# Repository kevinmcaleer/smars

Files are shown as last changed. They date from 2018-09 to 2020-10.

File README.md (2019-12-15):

# SMARS

Screwless Modular Assemblable Robotic System



## SMARSfan.com

Visit www.smarsfan.com for more information about this project. The site includes build instructions, videos, an interview with the designer and much more.

## SMARSLab & SMARS_Library

I've broken the SMARS code into two parts:

SMARS_Library is a component that can now be installed via

```console
pip install smars-library
```

 or visiting <https://pypi.org/project/smars-library/>

SMARSLab is a web-based application for controlling your SMARS robots. The aim it that this will support both bluetooth connected wheeled SMARS as well as ones running locally on a raspberry pi zero. It currently supports QUAD SMARS and there is a test `butil.py` app for testing bluetooth connectivity.
Visit <https://www.github.com/kevinmcaleer/smarslab> for more information.

## About this library

This library will enable you to get the quad robot walking and detecting its environment.

## Python Library now pulls from pip

There is now a SMARS Python library available via pip.

***Make sure you follow the instructions below to ensure the virtual environment is setup correctly and everything should work perfectly.***

## Setup a virtual environment

The best way to ensure all the right prerequisites are installed and the supported version of python is installed is by setting up a virtual environment for python.

To Install virtualenv:

* log on to your raspberry pi
* install virtualenv:

```console
sudo apt-get install virtualenv
```

* create a new virtual python environment:

```console
virtualenv -p python3 venv
```

* activate the new python environment:

```console
source venv/bin/activate
```

* install the pre-requisites:

```console
pip install -r requirements.txt
```

* to deactivate the environment once you have finished, type

```console
deactivate
```

## Files

```.
├── Documentation                   - All the Documents
│   └── SMARS Build Instructions
│       └── Build instructions.pdf  - PDF version of the build instructions
├── limb_setup.py                   - script for helping setup limbs on a QUAD SMARS
├── pinouts.md                      - Describes the pinouts for the PCA9685
├── README.md                       - this file
├── requirements.txt                - used by pip to install the prerequisites
├── S-Code.md                       - a code similar to G-Code for sending commands to a SMARS, work in progress
├── S-CodeParse.py                  - a parser for S-Code
├── Scratch 1.4
│   └── SMARSScratchDemo.sb         - an example Scratch 1.4 file for communicating with SMARS
├── ScratchListener.py              - the lister app for communicating with SMARS and Scratch
├── setup.sh                        - a shell script for setting up the code on a raspberry pi
├── SMARS_ultrasonic_demo
│   └── SMARS_ultrasonic_demo.ino   - a sample Arduino script for using the ultrasonic sensor
├── STL_Files                       - some STL files for modified tracks
│   ├── Track 18mm.png
│   ├── Track 18mm.stl
│   ├── Track 20.5mm 16h.stl
│   ├── Track 20.5mm.stl
│   ├── Track 205mm.stl
│   ├── Track 210mm.stl
│   └── Track.png
└── test                            - the test suite
    ├── test.md                     - test suite documentation
    ├── test.py                     - a simple test app for checking your SMARS setup
    └── test_suite.py               - the test suite used by Travis-CI to confirm build quality
```

## Scratch 1.4 Code

The Library now includes a sample Scratch 1.4 script that will enable you to control your SMARS Quad robot from the scratch environment. Please note you will need to enable the remote sensor control for this to work, by right clicking on the sensor and clicking on 'enable remote sensing'.

The Scratch demo script needs to communicate with the Python 'ScratchListener.py' code, and you will need to know the IP address of the computer running Scratch 1.4.

Note only Scratch 1.4 has the 'enable remote sensing' option available, Scratch 2.0 & Scratch 3.0 do not allow this, however you can still download and use Scratch 1.4 from the Scratch website: <http://scratch.mit.edu>

Link to thingiverse original model:
<https://www.thingiverse.com/thing:2662828>

Link to Quad version
<https://www.thingiverse.com/thing:2755973>

## Overview and Background

This robot is really easy and cheap to 3d print, build and program. It can be assembled without screws or soldering and it's modular so it can be adapted for different purposes. I'm Swiss, so I don't know American scholastic system but I would use SMARS in last year of middle school, high school or universities/ colleges. There is more "open electronics" compared to a Lego NXT or similar, so students need a few knowledges about security, electrical laws and so on. It can be use to improve software development skills, CAD skills or electronics skills, students can design their own modules and customize their SMARS.

### Programming SMARS

You can use most common small hardware platforms as the brains inside SMARS, the Arduino platform (and compatible) was used in the original design as its cheap, commonly available, and the tools for programming it are easy to use. For the quad version of the robot a Raspberry Pi Zero was used. The language commonly used on the Pi (and where it gets it name from) is Python. A library module has been written for both Arduino and Python to help you get started.

### Getting the Arduino IDE

Visit <http://www.arduino.cc> to download the latest Arduino Integrated Development Environment (IDE).

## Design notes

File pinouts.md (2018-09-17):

This is the pinout connections for the Raspberry Pi to PCA9685 Servo Driver:

PCA9685 GND to RPI Pin 39 (or Pin 6)
PCA9685 V+ to RPI Pin 2
PCA9685 SCL to RPI Pin 5 (SCL)
PCA9685 SDA to RPI Pin 3 (SDA)

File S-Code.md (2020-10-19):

# S-Code

S-code describes a set of codes used to communicate with a SMARS robot.

An example sent over bluetooth would be:

```
S111 3
```

This would move the robot forward 3 units. A unit is dependent on lots of things so its hard to define in the language.

## Generic Movement

```
100 - # Movement
101 - Move Forward
102 - Move backward
103 - Turn left
104 - Turn right
```

## Wheeled SMARS

 ```
 110 - # Movement
 111 - Move Forward
 112 - Move Backwards
 113 - Turn Left
 114 - Turn Right
```

## Quad Smars

 ```
 150 - # Quad SMARS movements
 151 - Walk Forward
 152 - Walk Backward
 153 - Turn Left
 154 - Turn Right
 155 - Stand Up
 156 - Sit Down
 157 - Clap
 158 - Wiggle
```

## Inputs

```
200 - # Inputs, sensors
210 - Light sensor
211 - get light level
220 - Line sensor
221 - get light level
230 - Ultrasonic sensor
231 - get distance from sensor
240 - # Battery Level
241 - get battery level
250 - # IMU
251 - Get position from IMU
252 - Get Compass Heading
```

## Outputs

```
300 - # output - sound and lights
400 - status
401 - get current status
500 - Other Motors (for future use)
501 - Move motor 1
```

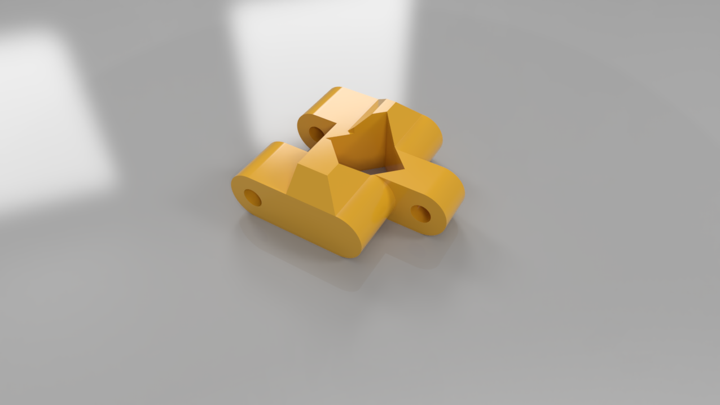
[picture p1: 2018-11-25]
STL_Files/Track 18mm.png

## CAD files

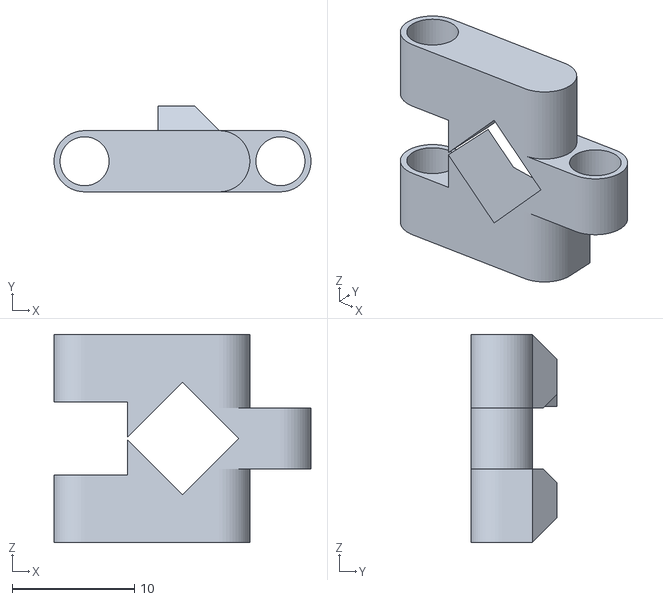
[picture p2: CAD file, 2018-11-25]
STL_Files/Track 210mm.stl
21.0 x 7.00 x 17.0

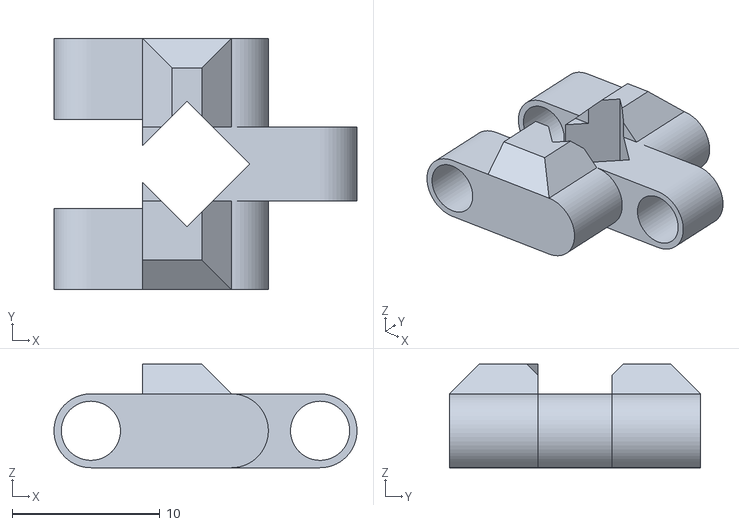
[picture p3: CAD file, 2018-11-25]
STL_Files/Track 20.5mm.stl
20.5 x 17.0 x 7.00

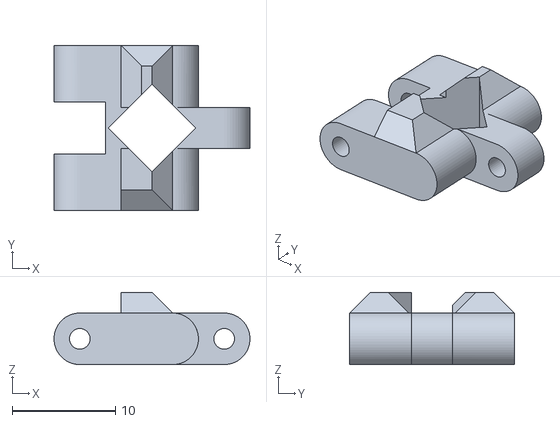
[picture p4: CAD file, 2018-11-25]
STL_Files/Track 18mm.stl
19.0 x 16.0 x 7.00

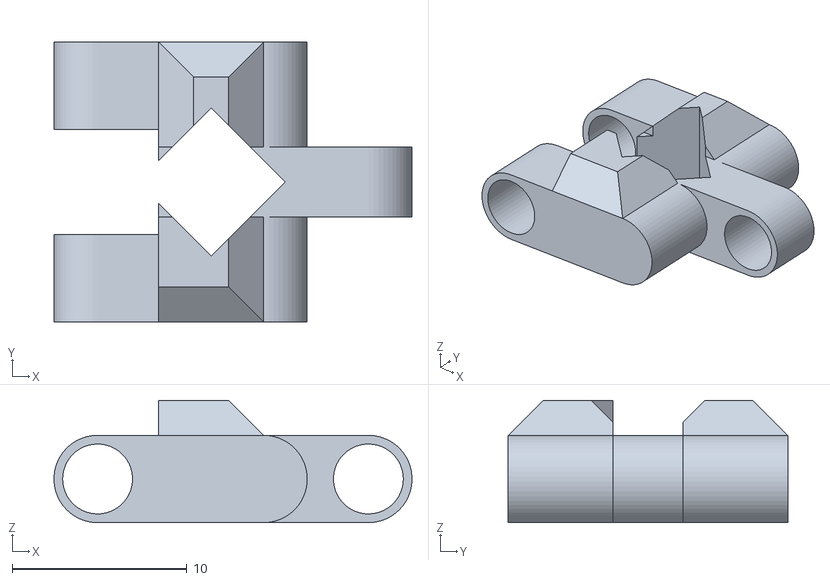
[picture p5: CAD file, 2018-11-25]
STL_Files/Track 20.5mm 16h.stl
20.5 x 16.0 x 7.00

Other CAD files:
STL_Files/Track 205mm.stl

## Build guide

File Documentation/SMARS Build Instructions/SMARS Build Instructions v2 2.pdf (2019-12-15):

# QUAD ROBOT WIRING DIAGRAM

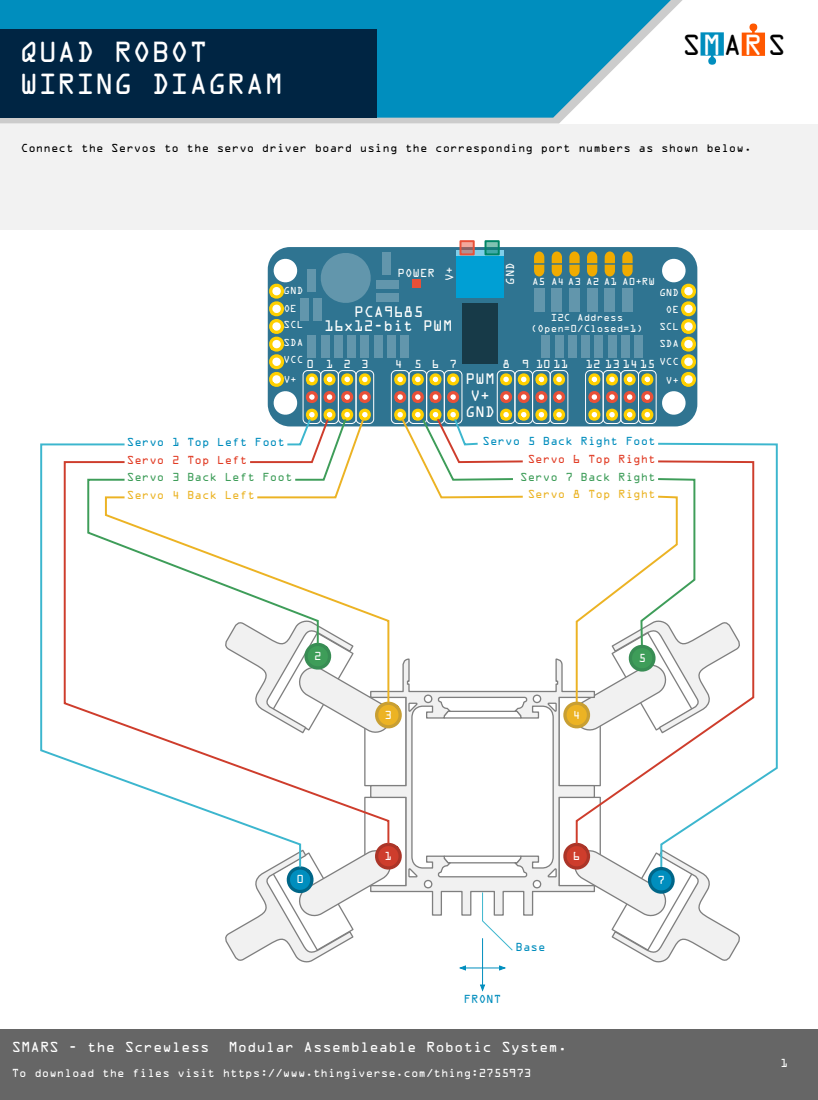
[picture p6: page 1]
SMAR S; SMARS - the Screwless; Modular Assembleable Robotic System.; GND; POWER; 16x12-bit PWM; PCA9685; PWM V+ GND; SCL; SDA; VCC; I2C Address (Open=0/Closed=1); Base; Servo 1 Top Left Foot; Servo 5 Back Right Foot; FRONT

Connect the Servos to the servo driver board using the corresponding port numbers as shown below.

Servo 2 Top Left
Servo 3 Back Left Foot
Servo 4 Back Left

Servo 6 Top Right
Servo 7 Back Right
Servo 8 Top Right

To download the files visit https://www.thingiverse.com/thing:2755973

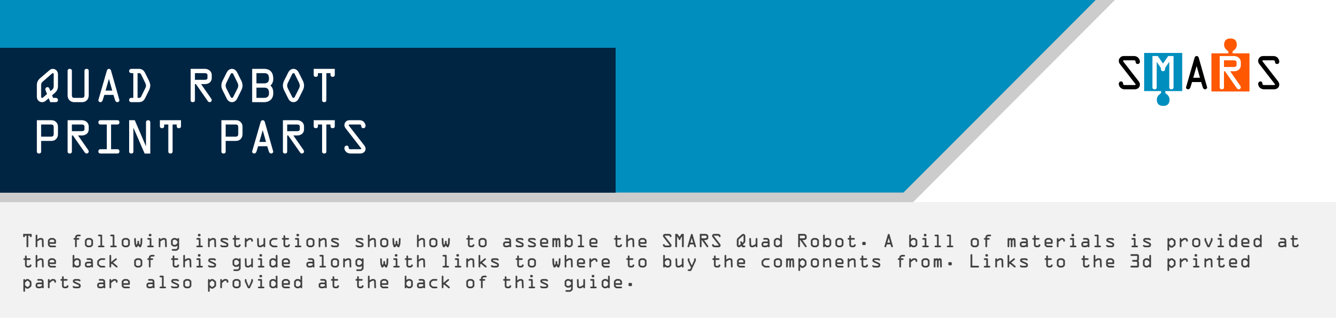
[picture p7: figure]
PRINT PARTS

1 | Print the frame
2 | Print the servo holders

Print 4x Servo holder & 4x Servo holder M (M is a mirror image of the servo holder)

SG90
Servo
Servo Holder | Servo Holder M
3 | Fit the servo into the servo holder

x8

4 Fit the servo holders into the frame

The following instructions show how to assemble the SMARS Quad Robot. A bill of materials is provided at the back of this guide along with links to where to buy the components from. Links to the 3d printed parts are also provided at the back of this guide.

# FITTING SERVOS

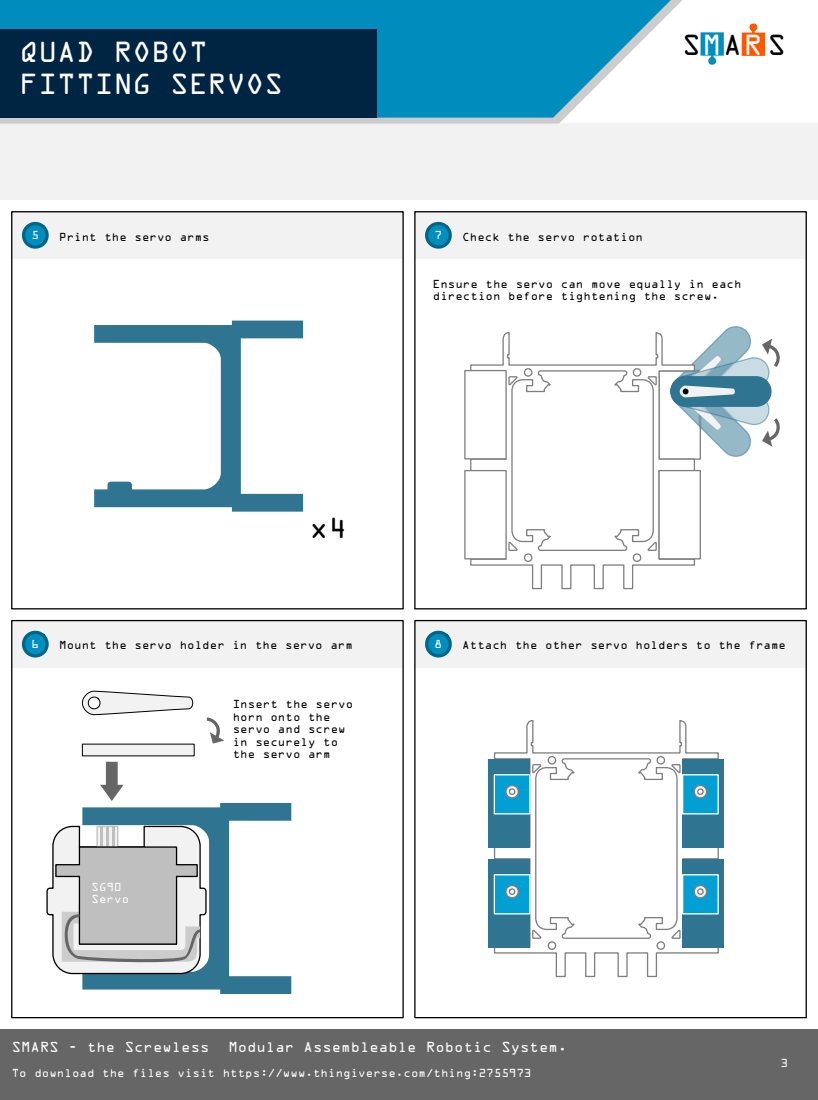
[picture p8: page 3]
Print the servo arms; Mount the servo holder in the servo arm; Check the servo rotation; Attach the other servo holders to the frame; SG90 Servo

Ensure the servo can move equally in each
direction before tightening the screw.

Insert the servo
horn onto the
servo and screw
in securely to
the servo arm

# FITTING THE FEET

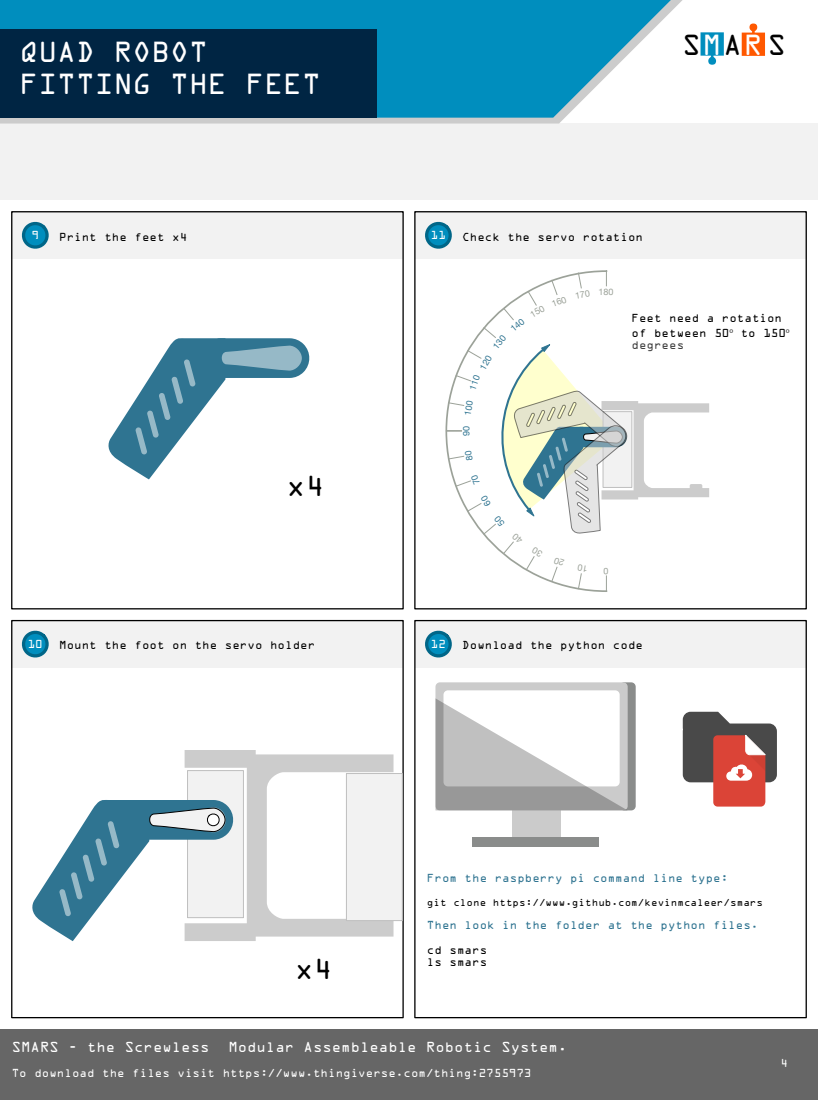
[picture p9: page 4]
Print the feet x4; Mount the foot on the servo holder; Check the servo rotation; Download the python code; cd smars ls smars

Feet need a rotation
of between 50º to 150º
degrees

From the raspberry pi command line type:

git clone https://www.github.com/kevinmcaleer/smars

Then look in the folder at the python files.

Connect the Raspberry pi Zero using the following pins:

PCA9685 GND to RPI Pin 39 (or Pin 6) - Black wire
PCA9685 V+ to RPI Pin 2 | - Red wire
PCA9685 SCL to RPI Pin 5 (SCL) | - Green wire
PCA9685 SDA to RPI Pin 3 (SDA) | - Blue wire

Note that the input voltage for the PCA9685 is 3.3v or 5v into the VCC. The V+ is for powering the servo motors and requires more power than the raspberry pi can provide, which is why it is separate. You can use a 9v battery to drive this, using the SMARS 9v case.

The raspberry pi communicates with the servo driver board using I2C, which only requires 2 wires: System Clock (SCL) and System Data (SDA). These are marked on servo driver board, and on pins 3 & 7 on the Raspberry Pi Zero.

# PI ZERO SETUP

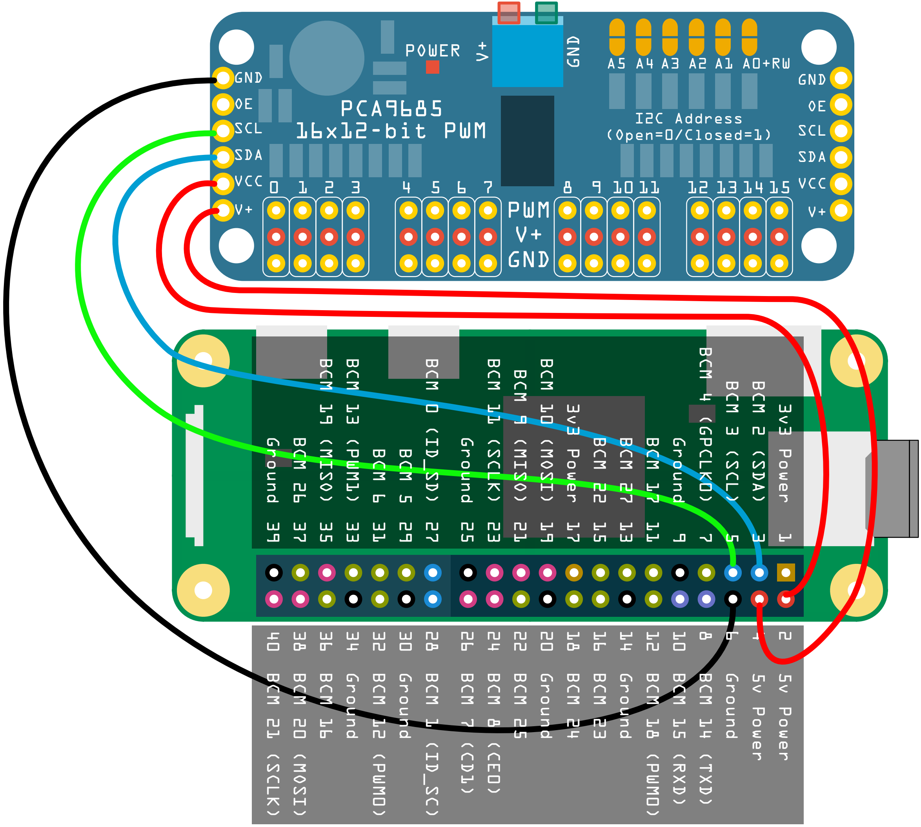
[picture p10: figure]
GND; POWER; 16x12-bit PWM; PCA9685; PWM V+ GND; SCL; SDA; VCC; I2C Address (Open=0/Closed=1); BCM 21 (SCLK); BCM 20 (MOSI); BCM 16; Ground; BCM 12 (PWM0); BCM 1 (ID_SC); BCM 7 (CD1); BCM 8 (CE0); BCM 25; BCM 24; BCM 23; BCM 18 (PWM0); BCM 15 (RXD); BCM 14 (TXD); 5v Power; 3v3 Power; BCM 3 (SCL); BCM 2 (SDA); BCM 4 (GPCLK0); BCM 22; BCM 27; BCM 17; BCM 10 (MOSI); BCM 9 (MISO); BCM 11 (SCLK); BCM 0 (ID_SD); BCM 6; BCM 5; BCM 19 (MISO); BCM 13 (PWM1); BCM 26

# RANGE OF MOTION

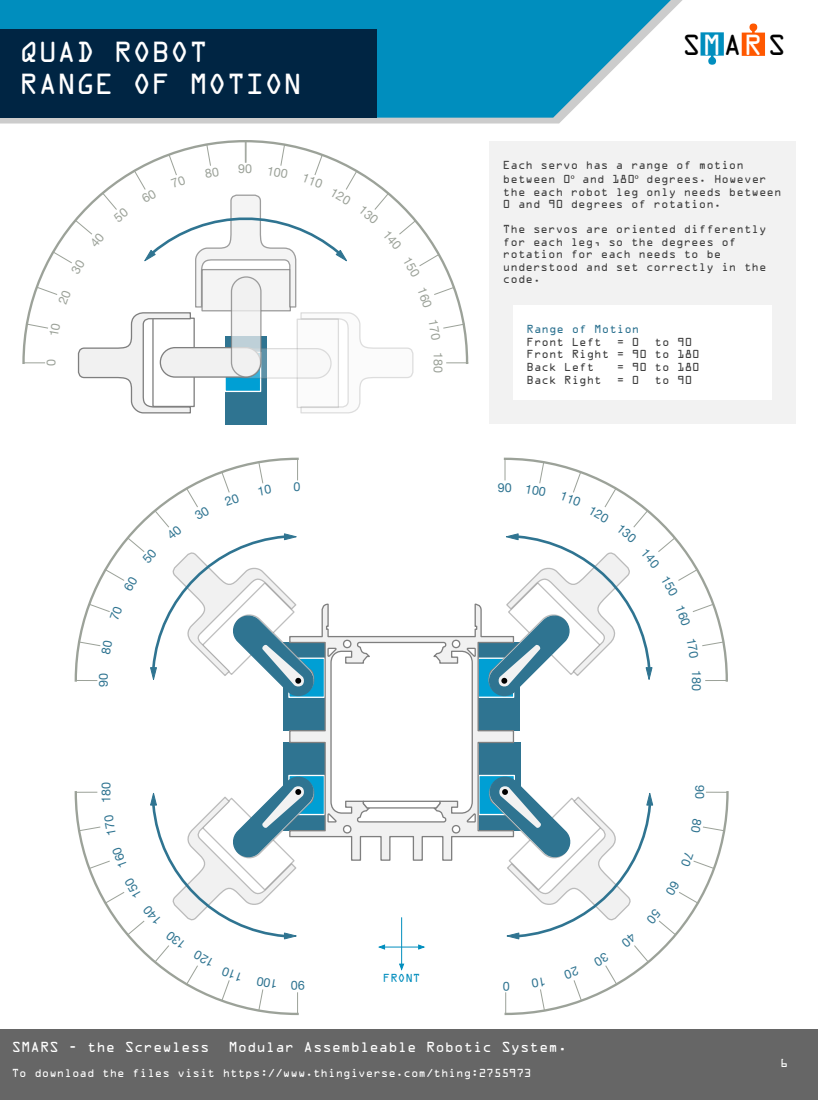
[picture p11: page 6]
Front Left; Back Left; Back Right; FRONT

Each servo has a range of motion
between 0º and 180º degrees. However
the each robot leg only needs between
0 and 90 degrees of rotation.

The servos are oriented differently
for each leg, so the degrees of
rotation for each needs to be
understood and set correctly in the
code.

Range of Motion
Front Right = 90 to 180

### Quad Robot Software Configuration

Once you’ve downloaded the python code you can begin checking the configuration of the servos:

### Python environment setup

The PCA9685 servo driver library is provided by Adafruit and needs to be installed before setup and using the SMARS Quad robot.

To download the adafruit servo library first logon to the Raspberry Pi and then type:

sudo apt-get install git build-essential python-dev cd ~
git clone https://github.com/adafruit/Adafruit_Python_PCA9685.git
cd Adafruit_Python_PCA9685
sudo python setup.py install

### Python is now setup for the servo

driver.

python limb_setup.py

### Use the menu to select the channel you want to configure. There are 16

channels, one for each servo.

The channels start at 0, and end at 15.

Menu
1) select channel
2) select angle
0) quit

current channel is: 0
current angle is: 0
enter number

Type ‘1’ to change the current channel.

Select Channel

currently selected channel is: 0
type channel number:, or q to return to the main menu

### Next, type 0 to configure channel 0

Type ‘1’ to change the current channel.

Select Channel

currently selected channel is: 0
type channel number:, or q to return to the main menu

### Next, type ‘0’ to configure channel 0

### Then type ‘q’ to return to the main

menu.

Menu
1) select channel
2) select angle
0) quit

current channel is: 0
current angle is: 0
enter number

### Type ‘2’ to set the angle for the

current channel.

Select Angle

current angle is: 0
Type angle to set servo to, or press q to exit90 90
Angle is: 90
Angle = | 90
Angle as a percentage = | 50.0
pulse = | 375
map Max = | 450
current angle: 90
Type angle to set servo to, or press q to exit

### Type ’90’ to set the angle to 90

Degrees.

### Then type ‘q’ to return to the main

menu.

### Repeat this until you have set each

limb correctly.

### Finally type ‘0’ to quit the limb setup

programme.

# SOFTWARE SETUP

### About this Guide

This guide was written by Kevin McAleer and is provided freely to the SMARS community.

### Social Media

If you haven’t already, please join the facebook community -https://www.facebook.com/groups/141101273276325/

# NEXT STEPS

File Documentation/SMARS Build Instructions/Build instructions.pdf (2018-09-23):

# QUAD ROBOT WIRING DIAGRAM

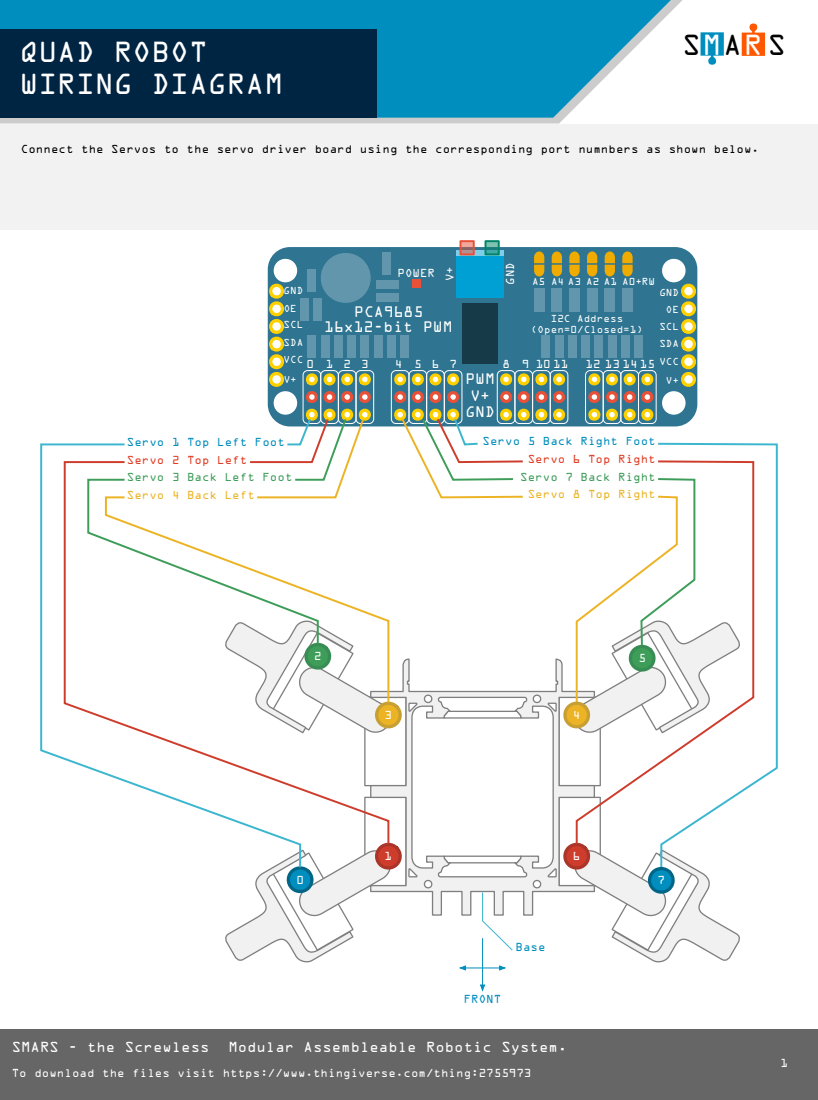
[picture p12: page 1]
SMAR S; SMARS - the Screwless; Modular Assembleable Robotic System.; GND; POWER; 16x12-bit PWM; PCA9685; PWM V+ GND; SCL; SDA; VCC; I2C Address (Open=0/Closed=1); Base; Servo 1 Top Left Foot; Servo 5 Back Right Foot; FRONT

Connect the Servos to the servo driver board using the corresponding port numnbers as shown below.

Servo 2 Top Left
Servo 3 Back Left Foot
Servo 4 Back Left

Servo 6 Top Right
Servo 7 Back Right
Servo 8 Top Right

To download the files visit https://www.thingiverse.com/thing:2755973

PRINT PARTS

1 | Print the frame
2 | Print the servo holders

Print 4x Servo holder & 4x Servo holder M (M is a mirror image of the servo holder)

SG90
Servo
Servo Holder | Servo Holder M
3 | Fit the servo into the servo holder

x8

4 Fit the servo holders into the frame

The following instructions show how to assemble the SMARS Quad Robot. A bill of materials is provided at the back of this guide along with links to where to buy the components from. Links to the 3d printed parts are also provided at the back of this guide.

# FITTING SERVOS

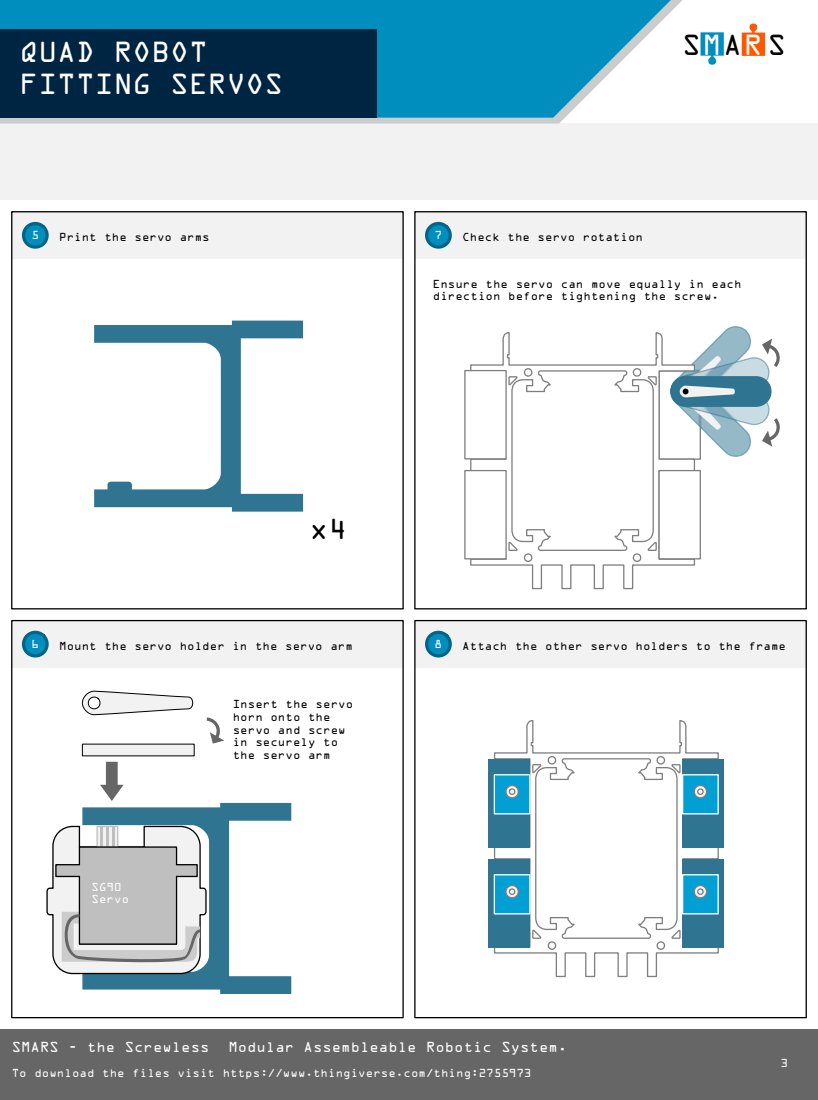
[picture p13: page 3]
Print the servo arms; Mount the servo holder in the servo arm; Check the servo rotation; Attach the other servo holders to the frame; SG90 Servo

Ensure the servo can move equally in each
direction before tightening the screw.

Insert the servo
horn onto the
servo and screw
in securely to
the servo arm

# FITTING THE FEET

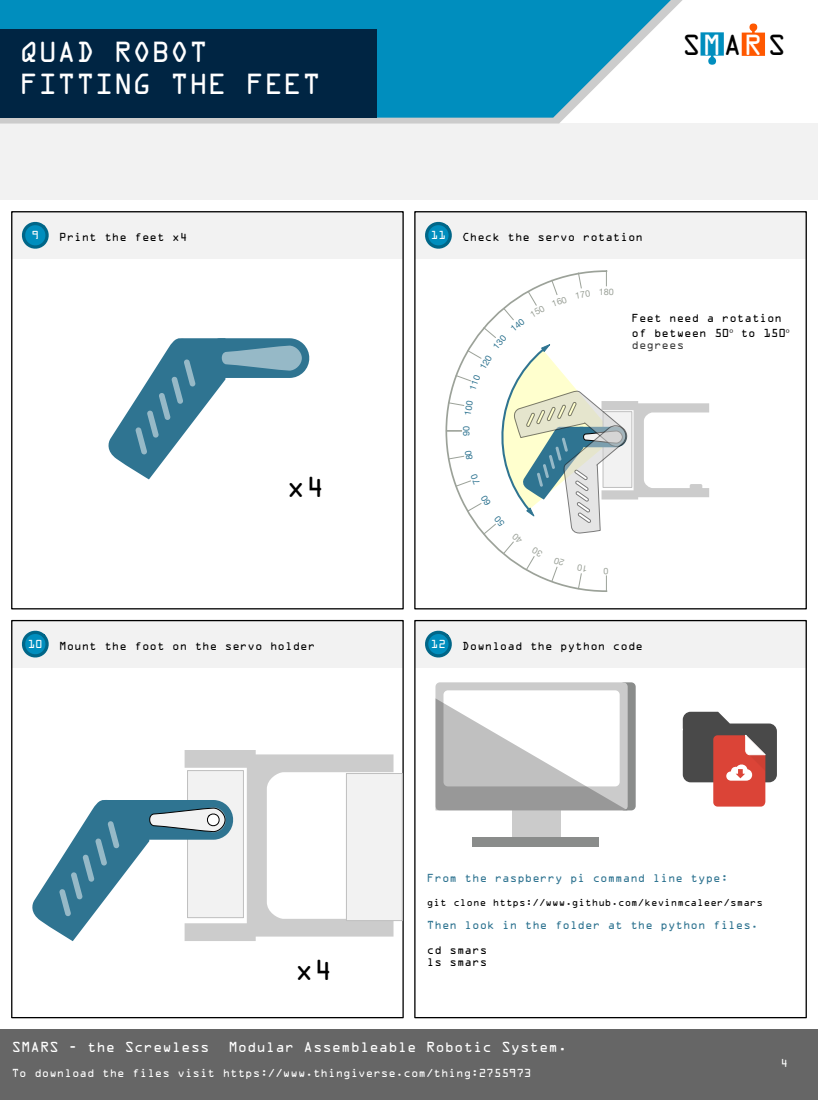
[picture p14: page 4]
Print the feet x4; Mount the foot on the servo holder; Check the servo rotation; Download the python code; cd smars ls smars

Feet need a rotation
of between 50º to 150º
degrees

From the raspberry pi command line type:

git clone https://www.github.com/kevinmcaleer/smars

Then look in the folder at the python files.

Connect the Raspberry pi Zero using the following pins:

PCA9685 GND to RPI Pin 39 (or Pin 6) - Black wire
PCA9685 V+ to RPI Pin 2 | - Red wire
PCA9685 SCL to RPI Pin 5 (SCL) | - Green wire
PCA9685 SDA to RPI Pin 3 (SDA) | - Blue wire

Note that the input voltage for the PCA9685 is 3.3v or 5v into the VCC. The V+ is for powering the servo motors and requires more power than the raspberry pi can provide, which is why it is separate. You can use a 9v battery to drive this, using the SMARS 9v case.

The raspberry pi communicates with the servo driver board using I2C, which only requires 2 wires: System Clock (SCL) and System Data (SDA). These are marked on servo driver board, and on pins 3 & 7 on the Raspberry Pi Zero.

# PI ZERO SETUP

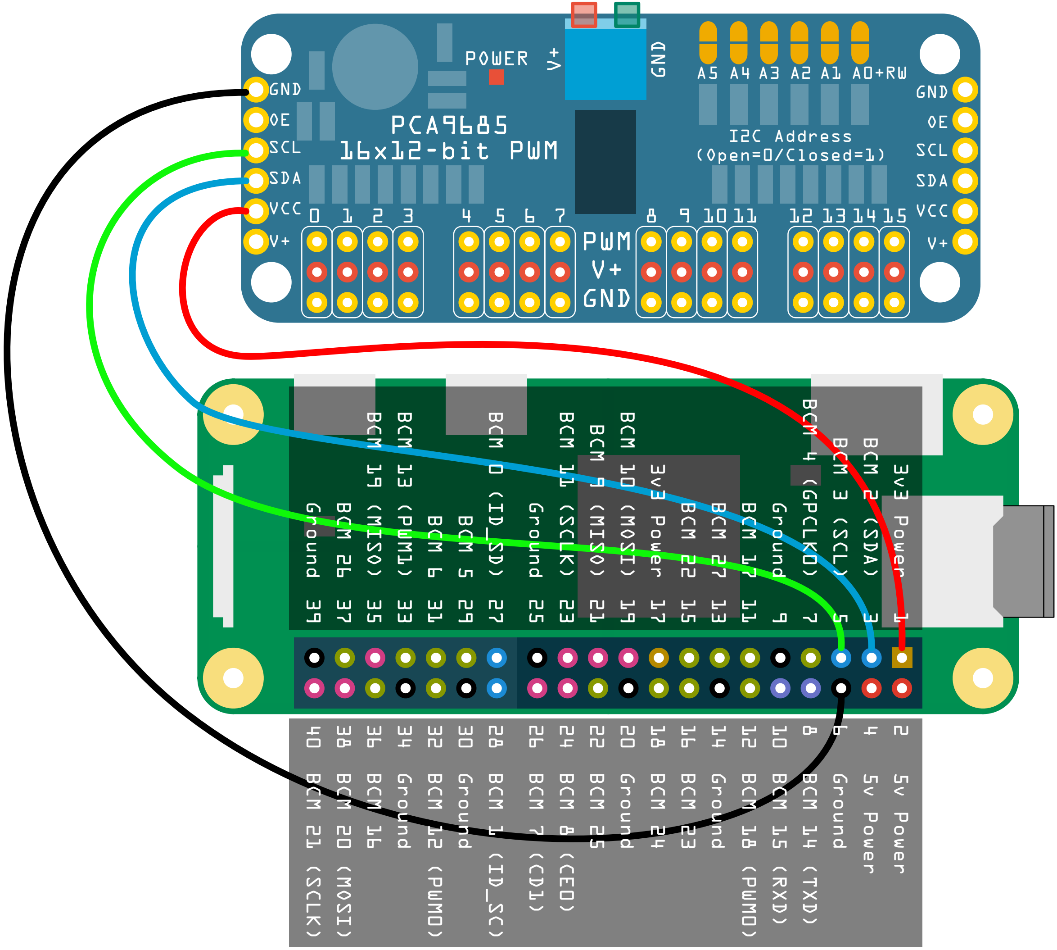
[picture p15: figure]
GND; POWER; 16x12-bit PWM; PCA9685; PWM V+ GND; SCL; SDA; VCC; I2C Address (Open=0/Closed=1); BCM 21 (SCLK); BCM 20 (MOSI); BCM 16; Ground; BCM 12 (PWM0); BCM 1 (ID_SC); BCM 7 (CD1); BCM 8 (CE0); BCM 25; BCM 24; BCM 23; BCM 18 (PWM0); BCM 15 (RXD); BCM 14 (TXD); 5v Power; 3v3 Power; BCM 3 (SCL); BCM 2 (SDA); BCM 4 (GPCLK0); BCM 22; BCM 27; BCM 17; BCM 10 (MOSI); BCM 9 (MISO); BCM 11 (SCLK); BCM 0 (ID_SD); BCM 6; BCM 5; BCM 19 (MISO); BCM 13 (PWM1); BCM 26

# RANGE OF MOTION

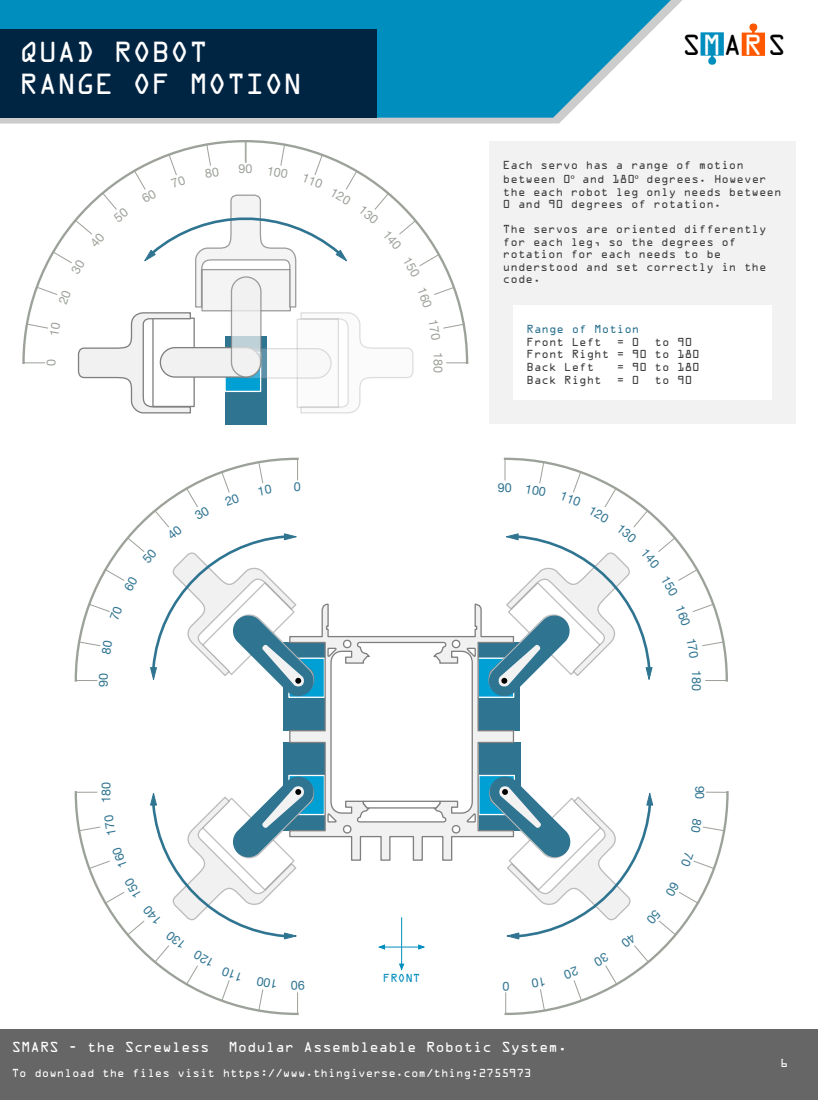
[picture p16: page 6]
Front Left; Back Left; Back Right; FRONT

Each servo has a range of motion
between 0º and 180º degrees. However
the each robot leg only needs between
0 and 90 degrees of rotation.

The servos are oriented differently
for each leg, so the degrees of
rotation for each needs to be
understood and set correctly in the
code.

Range of Motion
Front Right = 90 to 180

### Quad Robot Software Configuration

Once you’ve downloaded the python code you can begin checking the configuration of the servos:

### Python environment setup

The PCA9685 servo driver library is provided by Adafruit and needs to be installed before setup and using the SMARS Quad robot.

To download the adafruit servo library first logon to the Raspberry Pi and then type:

sudo apt-get install git build-essential python-dev cd ~
git clone https://github.com/adafruit/Adafruit_Python_PCA9685.git
cd Adafruit_Python_PCA9685
sudo python setup.py install

### Python is now setup for the servo

driver.

python limb_setup.py

### Use the menu to select the channel you want to configure. There are 16

channels, one for each servo.

The channels start at 0, and end at 15.

Menu
1) select channel
2) select angle
0) quit

current channel is: 0
current angle is: 0
enter number

Type ‘1’ to change the current channel.

Select Channel

currently selected channel is: 0
type channel number:, or q to return to the main menu

### Next, type 0 to configure channel 0

Type ‘1’ to change the current channel.

Select Channel

currently selected channel is: 0
type channel number:, or q to return to the main menu

### Next, type ‘0’ to configure channel 0

### Then type ‘q’ to return to the main

menu.

Menu
1) select channel
2) select angle
0) quit

current channel is: 0
current angle is: 0
enter number

### Type ‘2’ to set the angle for the

current channel.

Select Angle

current angle is: 0
Type angle to set servo to, or press q to exit90 90
Angle is: 90
Angle = | 90
Angle as a percentage = | 50.0
pulse = | 375
map Max = | 450
current angle: 90
Type angle to set servo to, or press q to exit

### Type ’90’ to set the angle to 90

Degrees.

### Then type ‘q’ to return to the main

menu.

### Repeat this until you have set each

limb correctly.

### Finally type ‘0’ to quit the limb setup

programme.

# SOFTWARE SETUP

### About this Guide

This guide was written by Kevin McAleer and is provided freely to the SMARS community.

### Social Media

If you haven’t already, please join the facebook community -https://www.facebook.com/groups/141101273276325/

# NEXT STEPS

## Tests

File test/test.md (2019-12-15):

# Unit Tests

## def set_servo_pulse(channel, pulse)

1. Check that channel is a positive integer (between 0 and 15)
1. Check that pulse is a number between 0 and 4096

## Class leg()

### def moveTo(self, position)

check that position is valid

---

### def setAngle(self, angle)

check that angle is between 0 and 180

---

## class SmarsRobot(object)

### def setName(self, name)

check that name doesn't exceed 20 characters

---

### def walkForward(self, steps)

check that steps is a valid integer, and is less than 100

---

### def walkBackward(self, steps)

check that steps is a valid integer, and is less than 100

---

### def clap(self, clap_count)

check that clap_count is less than 100

---

### def wiggle(self, wiggle_count)

check that wiggle_count is less than 100

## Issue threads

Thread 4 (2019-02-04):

Wiring docs need serious review.

jetdillo, 2019-02-04:
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
The servo wiring diagram needs some serious attention. The colors make sense, but the numbering is way off. This isn't even an off-by-one error. The blue line labeled "servo 5" actually connects to 7  and "servo8" leads to 4. Maybe your chart/diagram software auto-numbering went a little wonky and mislabeled things ? Anyway, please check it out.

kevinmcaleer, 2019-03-23:
I'm looking into this now. You're quite correct, not sure what happened, but I'll update, check and republish.

jetdillo, 2019-03-24:
Cool. Thanks for looking into it!

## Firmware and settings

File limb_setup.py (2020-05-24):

#Leg setup

VERSION = "1.0"
# setup leg 1:

# from SMARS_Library import *
from smars_library.smars_library import SmarsRobot, Leg
import smars_library.smars_library

channel_number = 1
l1 = Leg(name="limb test", channel=channel_number,  leg_minangle=0, leg_maxangle=180, invert=False)
# l1.name = "left_leg_front"
# l1.channel = channel_number
# l1.leg_minAngle = 0
# l1.leg_maxAngle = 180
# l1.invert = False

def menu():
    """ display the main menu """
    print("")
    print("*** SMARS Limb setup, Version ", VERSION, "***")
    print("")
    print("Menu")
    print("----")
    print("") 
    print("Select:")
    print("1) Channel")
    print("2) Angle")
    print("0) Quit")
    print("")

channel_number = 0
def select_channel():
    global channel_number
    global l1
    print("")
    print("")
    print("CHANNEL")
    print("-------------------------")
    print("")
    print("Currently selected channel is:", channel_number)
    print("")
    print("Select new channel.")
    key = ""
    ch = 0
    #  need to make this loop exit once the channel number is selected and "q" pressed
    while key != "q":
        key = input("Type channel number:, or q to return to the main menu")
        print("")
        print(key)
        if key == "q":
            print("")
        else:
            ch = int(key)
            if ch >= 16:
                print("sorry that channel number is too high, needs to be between 0 and 15")
            else:
                channel_number = int(ch)
                l1.channel = channel_number
                l1.show()

angle = 0

def show_status():
    """
    Shows the currently selected channel and angle
    """
    print("")
    print("[current channel is:", l1.channel,"]:[current angle is:", angle,"]")
    print("")

def select_angle():
    """ change the current angle """
    global angle
    print("Select Angle")
    print("------------")
    print("")
    print("current angle is:", angle)

    # l1.setAngle(angle)
    key = ""
    while key != "q":
        key = input("Type angle to set servo to, or press q to exit")
        print(key)
        if key == "q":
            print("")
        else:
            # if raw_input ==
            # angle = angle + 10
            angle = int(key)
            l1.setangle(angle)
            print("current angle:", angle)

menu_key = ""
# show Menu until quit
while menu_key != "0":
    menu()
    show_status()
    menu_key = input("enter choice ")

    if (menu_key == "1") or (menu_key == "c"):
        select_channel()
    if (menu_key == "2") or (menu_key == "a"):
        select_angle()
    if (menu_key == "0") or (menu_key == "q"):
        print("Good bye!")

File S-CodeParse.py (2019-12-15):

"""
S-code Parser
"""

from smars_library.smars_library import SmarsRobot, Leg
import smars_library.smars_library as sl
import time

def readLine(line):

    sm = SmarsRobot()
    sm.setname("Quaddy")
    sm.type = "Quad"

    if line[0] == 's101': # Move Forward
        sm.walkforward(100)
    if line[0] == 's102': # Move Backward
        sm.walkbackward(100)
    if line[0] == 's103': # Turn left
        sm.turnleft()
    if line[0] == 's104': # Turn right
        sm.turnright()
    if line[0] == 's155': # Stand Up
        sm.stand()
    if line[0] == 's156': # Sit down
        sm.sit()
    if line[0] == 's157': # Clap
        print("line count: ", len(line))
        if len(line) <= 1:
            clap_count = 3
        else:
            clap_count = int(line[1]) # convert str to int
        sm.clap(clap_count)
    if line[0] == 's158': # Wiggle
        print("line count:", len(line))
        if len(line) <= 1:
            wiggle_count = 3
        else:
            wiggle_count = int(line[1]) # convert str to int
        sm.wiggle(wiggle_count)
# Main
keywords = ""
while keywords != "quit":

    key = input("# ")
    keywords = key.split()

    for items in keywords:
        print(items)

    readLine(keywords)

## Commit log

2018-09-17 fixed legs
2018-09-17 fixed legs typo
2018-09-17 fixed leg bug
2018-09-17 added leg debug messages
2018-09-17 print typo
2018-09-17 Added pwm init
2018-09-17 sitting down legs
2018-09-17 hard coded 0 in leg init
2018-09-17 corrected leg settings
2018-09-17 fixed all legs
2018-09-17 added legs and feet
2018-09-17 leg reset bug fixed
2018-09-23 used wrong comparison operators
    [limb_setup.py]
2018-09-23 fixed feet and legs on sit and stand
    [test.py]
2018-09-23 updated SMARS_Library leg up and down functions to use new setAngle function.
2018-09-23 Removed debug print statements from setAngle
2018-09-23 fixing leg and feet enumeration
2018-09-23 enumerating legs
2018-09-23 speed up and added print to continuous check
2018-09-30 added all feet and leg continuous tests
2018-09-30 Fixed continous leg test
    [test.py]
2018-09-30 fixed continous leg test bug
    [test.py]
2018-09-30 leg test debuging
2018-09-30 fixed leg ordering constants
    [test.py]
2018-09-30 fixed leg up
2018-09-30 added stretch leg tests
2018-09-30 moved setBody and setStretch to leg class
2018-09-30 removed the wrong leg loop from setBody and setStretch
2018-09-30 updated left leg back to invert False
2018-09-30 changed left front leg back to True
2018-09-30 fixed leg
2018-09-30 print angle to debug setSwing
2018-09-30 print angle
2018-09-30 added leg name to setAngle error
2018-09-30 replaced legs with feet
2018-10-06 added leg tick()
2018-10-06 updated front leg range to stop clashing with ultrasound sensor.
2018-10-06 front left leg cycle
2018-10-06 all legs!
2018-10-06 updated all legs
2018-10-07 just one leg
2018-10-07 reinstated all legs in walk
2018-10-07 right leg logic
2018-10-07 1 leg
2018-10-07 2 legs
2018-10-07 3 legs
2018-10-07 leg debug message added
2018-10-07 right leg logic added.
2018-10-07 all 4 legs
2018-10-07 added step count to walkForwward, tidied up some print statements.
2018-10-10 Added Arduino code.
2018-10-17 Arduino ultrasonic demo
2018-11-24 added Track Variations
    [Track 18mm.stl, Track 20.5mm 16h.stl, Track 20.5mm.stl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]
2018-11-25 added Track Variations
    added test.md
    SPRINT1 Feature Complete@
    [Track 18mm.stl, Track 20.5mm 16h.stl, Track 20.5mm.stl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]
2018-11-25 Cleaned up Folder and added some files to ignore in .gitignore
    [Track 18mm.stl, Track 20.5mm 16h.stl, Track 20.5mm.stl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]
2018-11-25 Cleaned up Folder and added some files to ignore in .gitignore
    - Tidied up Smars_library.py code and added pydoc comments.
    [Track 18mm.stl, Track 20.5mm 16h.stl, Track 20.5mm.stl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]
2018-11-25 Added Clap function - Added Clap to Test.py - Added Clapcount parameter - Fixed typo in clapcount - Added Clap delay - Quicker clap
    [test.py]
2018-11-25 switched round the up to down on wiggle
2018-11-25 corrected leg down bug
2018-11-25 corrected typo with sit stand and clap
    [S-CodeParse.py]
2018-11-25 added clapcount array fix
    [S-CodeParse.py]
2018-11-25 added Stand, Sit and Clap
    - corrected typo with sit stand and clap
    - added parameter for clap
    - converted str to int for clapcount
    - added clap count default
    - added clapcount array fix
    - added line count debug message
    - added elif on readline
    added elif on readline
    fixed else bug
    [S-CodeParse.py]
2018-11-25 Added Wiggle function
    Added a delay to wiggle
    Added delay to end of wiggle
    changed down to up
    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
    [test.py]
2018-12-02 corrected other function name references
    [test_suite.py]
2018-12-02 added import leg.setAngle
2018-12-25 added adafruit pca9685 driver library
2018-12-25 enable i2c-dev interface
2018-12-25 added sudo to i2c enabler
2018-12-25 added invert = False to leg class
2018-12-25 corrected the leg initiator
2018-12-25 updated leg class
2020-05-24 fixed relative import issue
    [test.py]
2020-10-19 added power subsystems omnigraffle
